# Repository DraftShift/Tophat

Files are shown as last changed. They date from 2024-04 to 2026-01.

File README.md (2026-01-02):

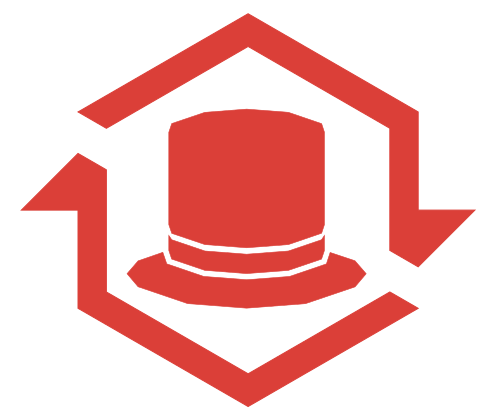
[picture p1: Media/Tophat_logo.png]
#  Tophat 


&nbsp;&nbsp;&nbsp;&nbsp;&nbsp;&nbsp;


## 🌐 Official Website

StealthChanger now has an official website!

👉 **https://stealthchanger.com** 

##
Currently there is only a simplified print it yourself version. This is meant for people not wanting to invest in more extrusions and side plates. you simply have to print the parts. and you can reuse your old top plate and corner pieces.

NOTE, a fully parametric design using extrusions is under design though it will take longer to finalise. The next design will have a bigger focus on adding things like lights, can wiring and other QOL / fancypants features.

### The current height is 200mm tall, check if this is good enough for your purposes!

## Printed part BOM
### 350 - 300
- 56x M3 heat inserts
- 24x M3x10mm SHCS
- 56x M3x8mm SHCS
- 24x M3 T-nut hammerhead

### 250
- 56x M3 heat inserts
- 24x M3x10mm SHCS
- 48x M3x8mm SHCS
- 16x M3 T-nut hammerhead

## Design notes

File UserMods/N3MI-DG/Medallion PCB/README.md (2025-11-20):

# RGB PCB for Stealthchanger Medallion
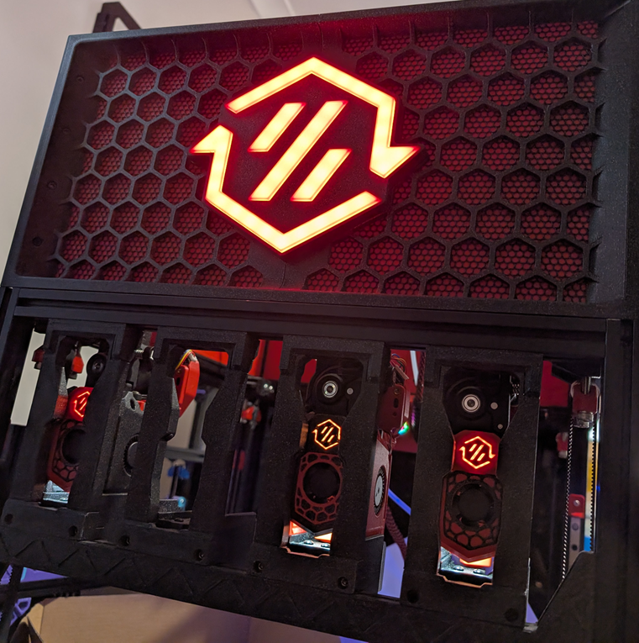
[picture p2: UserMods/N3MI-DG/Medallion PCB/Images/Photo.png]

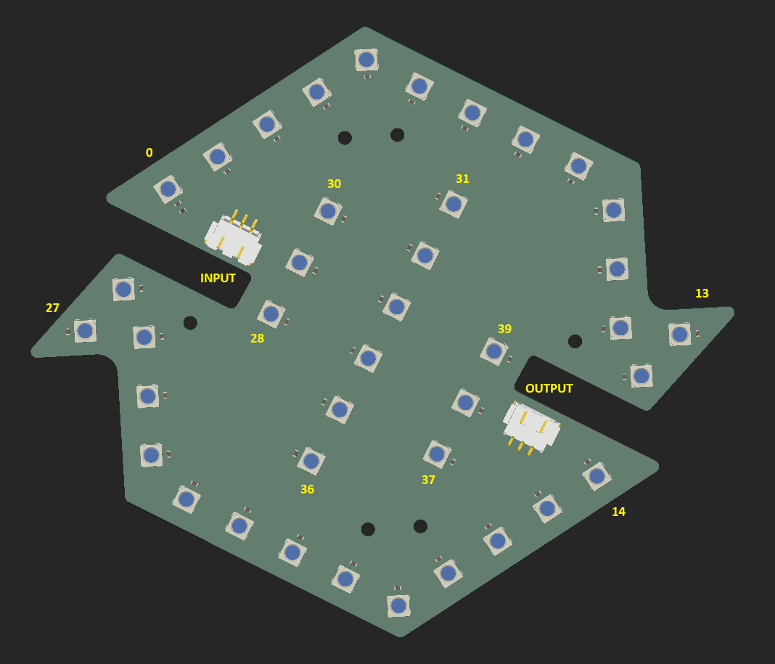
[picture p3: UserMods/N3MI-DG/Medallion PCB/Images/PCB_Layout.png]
PCB Layout


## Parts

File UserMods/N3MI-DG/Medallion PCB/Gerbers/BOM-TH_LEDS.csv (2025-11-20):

Comment | Designator | Footprint | LCSC | Quantity
C0.1uF | C1,C10,C11,C12,C13,C14,C15,C16,C17,C18,C19,C2,C20,C21,C22,C23,C24,C25,C26,C27,C28,C29,C3,C30,C31,C32,C33,C34,C35,C36,C37,C38,C39,C4,C40,C5,C6,C7,C8,C9 | C_0603_1608Metric | C14663 | 40
Conn_01x03_Socket | J1,J2 | JST_XH_S3B-XH-SM4-TB_1x03-1MP_P2.50mm_Horizontal | C161860 | 2
R470 | R1 | R_0603_1608Metric | C23179 | 1
SK6812 | D1,D10,D11,D12,D13,D14,D15,D16,D17,D18,D19,D2,D20,D21,D22,D23,D24,D25,D26,D27,D28,D29,D3,D30,D31,D32,D33,D34,D35,D36,D37,D38,D39,D4,D40,D5,D6,D7,D8,D9 | LED_SK6812_PLCC4_5.0x5.0mm_P3.2mm | C5181320 | 40

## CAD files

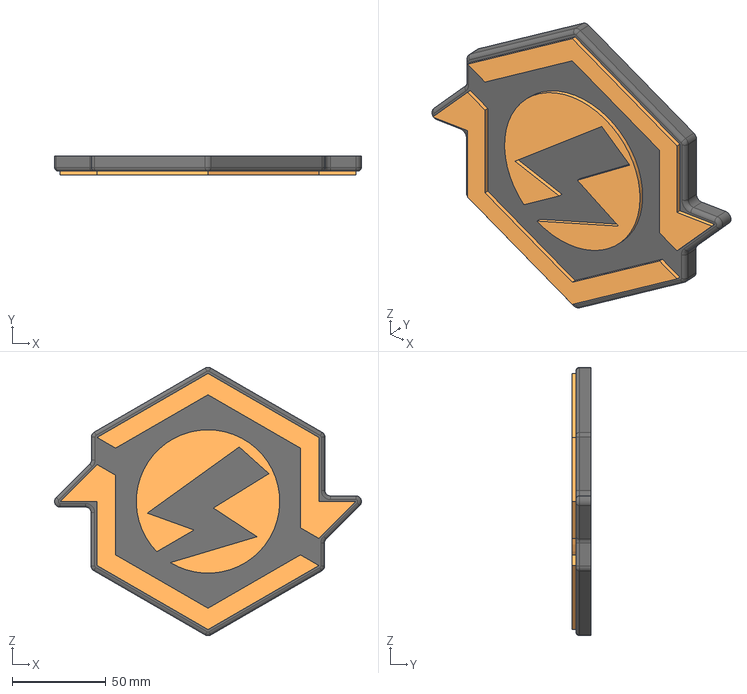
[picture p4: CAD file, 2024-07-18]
Printed version/CAD/Medalion Sovol.step
164.0 x 10.0 x 143.4 mm

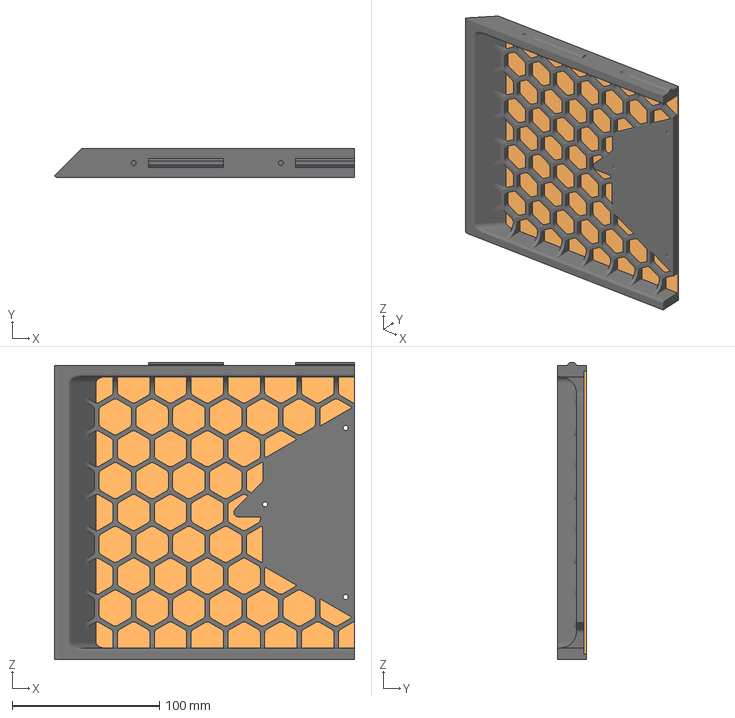
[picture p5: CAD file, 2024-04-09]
Printed version/STLs/250/Side_B_250_x4.3mf
203.8 x 20.0 x 202.0 mm

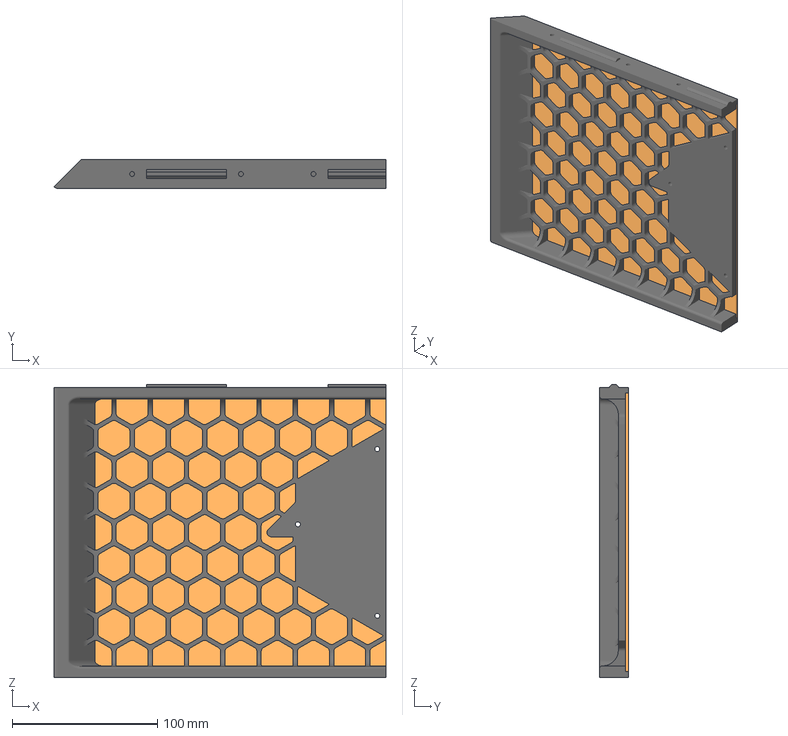
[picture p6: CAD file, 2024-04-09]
Printed version/STLs/300/Side_B_300_x4.3mf
228.8 x 20.0 x 202.0 mm

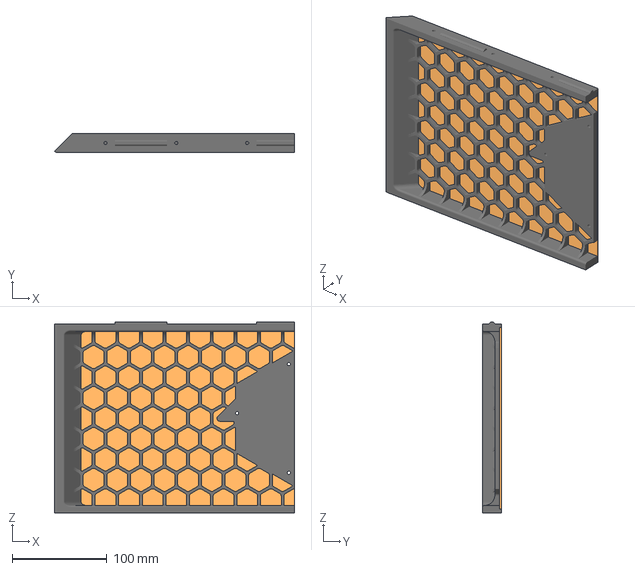
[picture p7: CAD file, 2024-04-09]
Printed version/STLs/350/Side_B_350_x4.3mf
253.8 x 20.0 x 202.0 mm

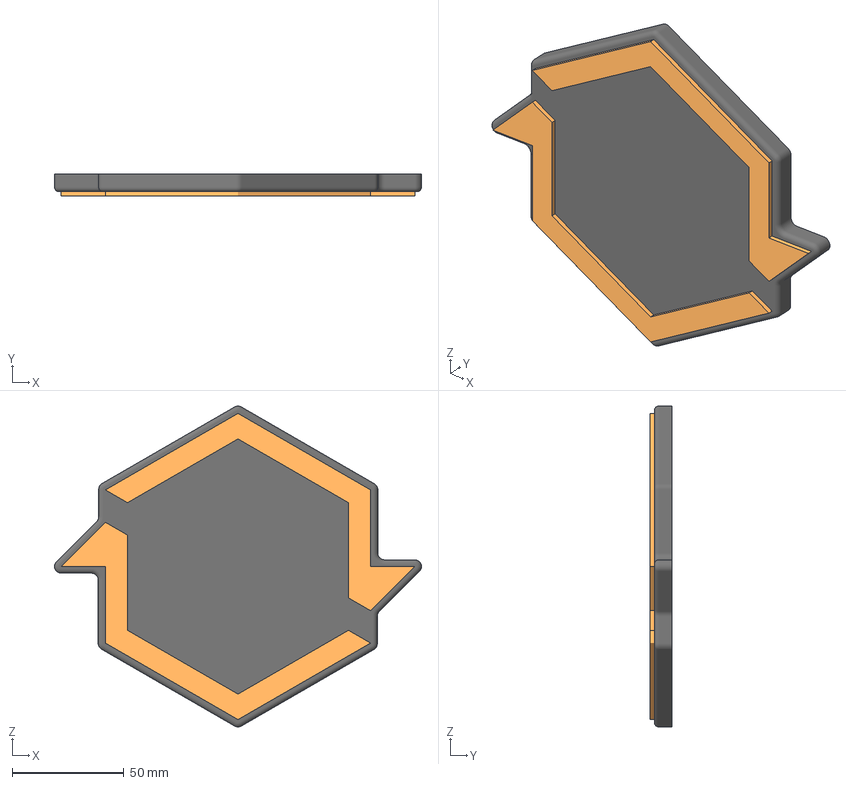
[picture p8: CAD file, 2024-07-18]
Printed version/STLs/Medalion Blank.3mf
164.0 x 10.0 x 143.4 mm

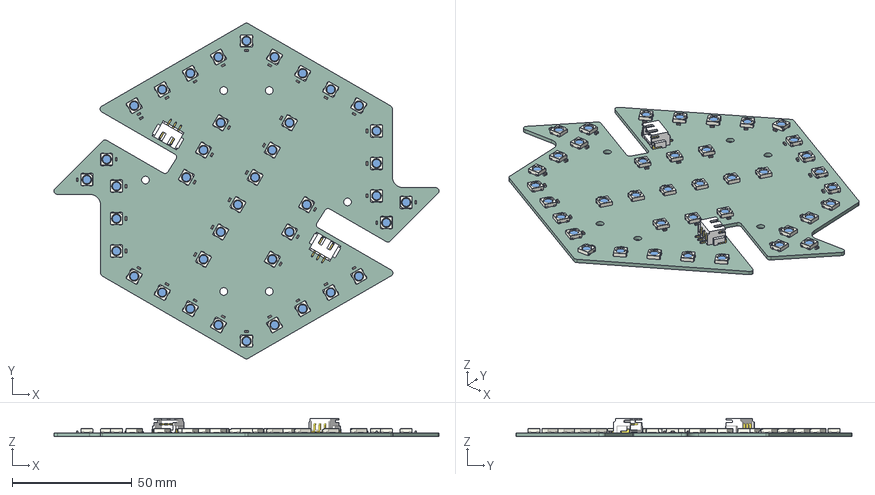
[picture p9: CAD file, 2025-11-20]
UserMods/N3MI-DG/Medallion PCB/Source/TH_LEDS.step
160.8 x 140.2 x 7.59 mm
LED_SK6812_PLCC4_5.0x5.0mm_P3.2mm x 40
C_0603_1608Metric x 40
S3B-XH-SM4-TB x 2
R_0603_1608Metric
TH_LEDS_PCB

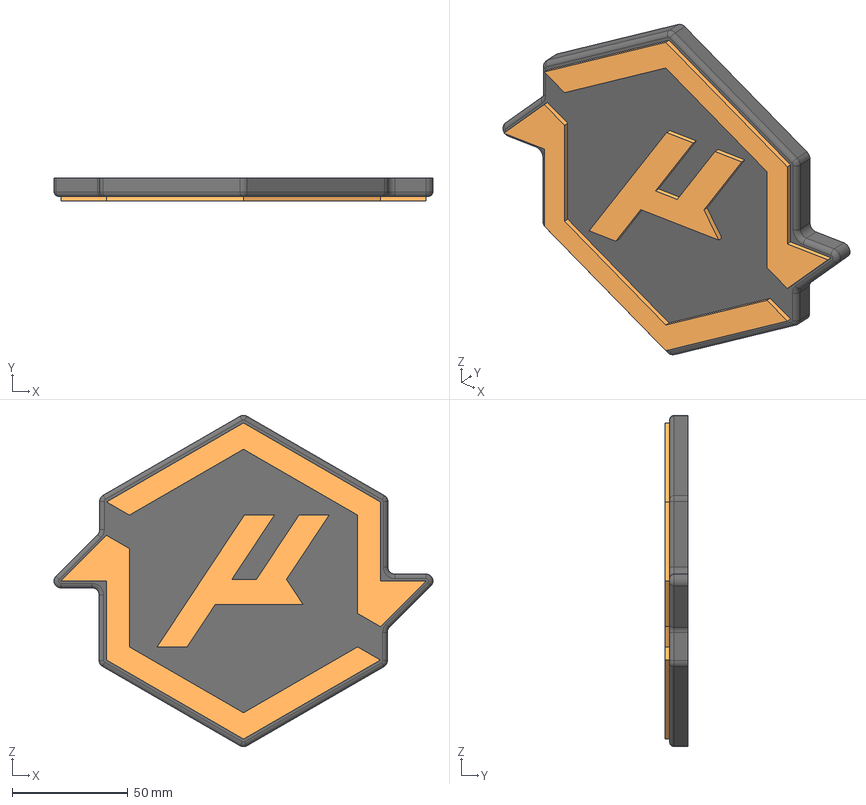
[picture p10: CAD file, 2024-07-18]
Printed version/CAD/Medalion Micron.step
164.0 x 10.0 x 143.4 mm

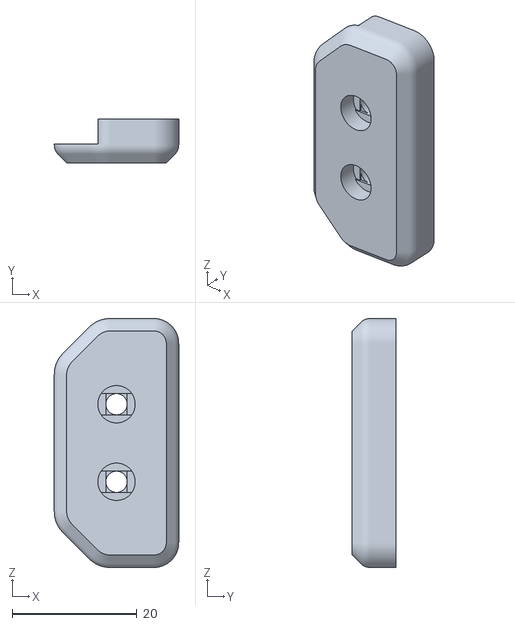
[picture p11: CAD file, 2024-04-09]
Printed version/STLs/Midclip_[a]_x4.stl
20.0 x 7.00 x 40.0

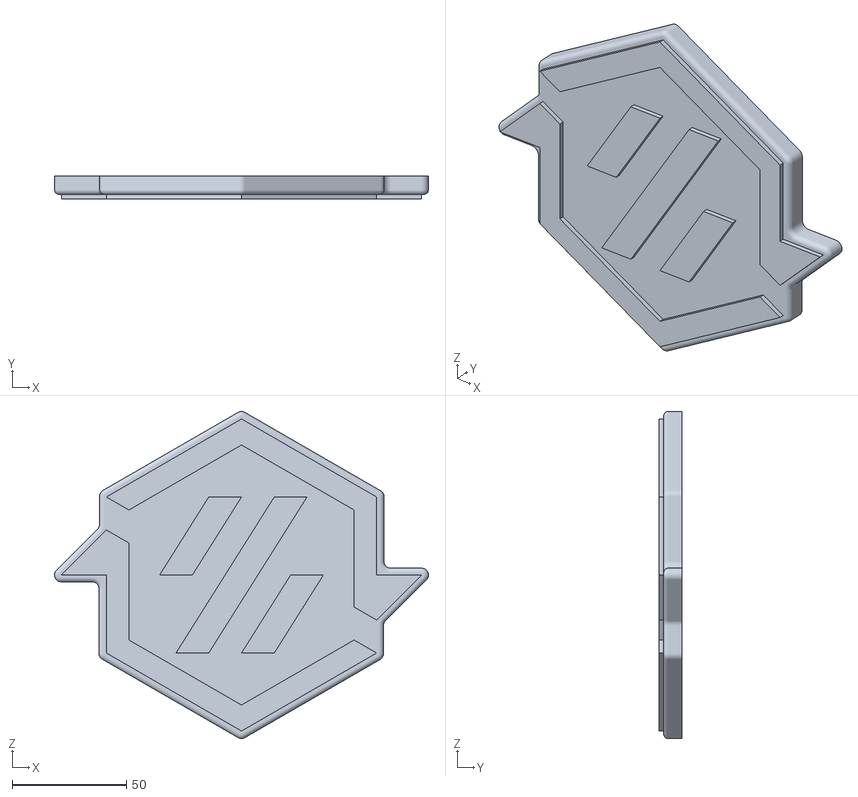
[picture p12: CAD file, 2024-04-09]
Printed version/STLs/Medalion.stl
164.0 x 10.0 x 143.4

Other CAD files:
Printed version/STLs/250/Side_A_250_x4.3mf
Printed version/STLs/300/Side_A_300_x4.3mf
Printed version/STLs/350/Side_A_350_x4.3mf
Printed version/CAD/Medalion Archetype.step
Printed version/CAD/Medalion Blanks.step
Printed version/CAD/Printed_tophat_Medalion.step
Printed version/CAD/Printed_tophat_Medalion.f3d
Printed version/STLs/Medalion Archetype.3mf
Printed version/STLs/Medalion Micron.3mf
Printed version/STLs/Medalion Sovol.3mf

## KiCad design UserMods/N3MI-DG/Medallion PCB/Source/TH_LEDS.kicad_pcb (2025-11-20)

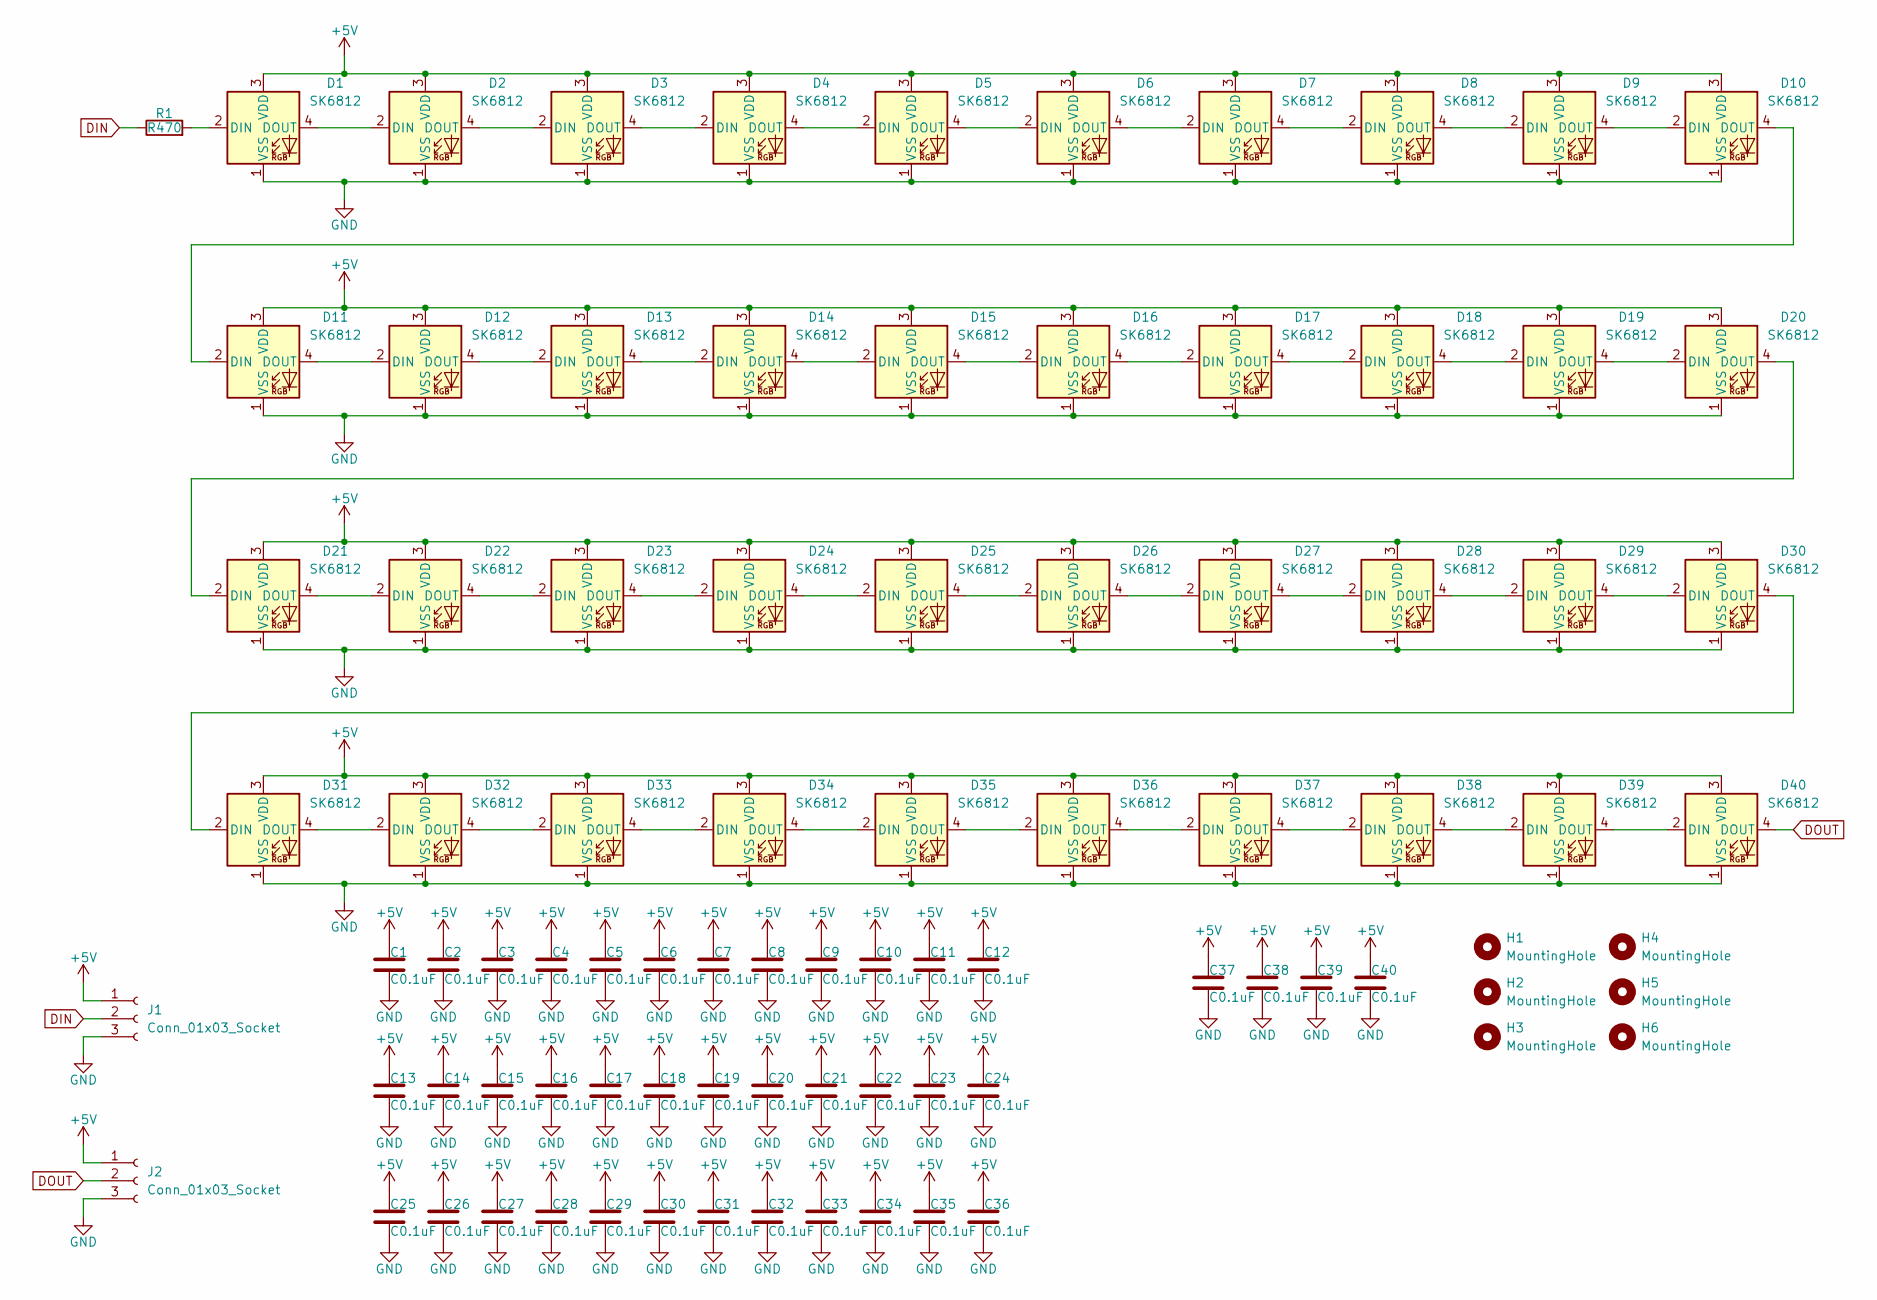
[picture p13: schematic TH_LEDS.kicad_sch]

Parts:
C1, C2, C3, C4, C5, C6, C7, C8, C9, C10, C11, C12, C13, C14, C15, C16, C17, C18, C19, C20, C21, C22, C23, C24, C25, C26, C27, C28, C29, C30, C31, C32, C33, C34, C35, C36, C37, C38, C39, C40: C0.1uF; C_0603_1608Metric
D1, D2, D3, D4, D5, D6, D7, D8, D9, D10, D11, D12, D13, D14, D15, D16, D17, D18, D19, D20, D21, D22, D23, D24, D25, D26, D27, D28, D29, D30, D31, D32, D33, D34, D35, D36, D37, D38, D39, D40: SK6812; LED_SK6812_PLCC4_5.0x5.0mm_P3.2mm
H1, H2, H3, H4, H5, H6: MountingHole; MountingHole_3.2mm_M3_DIN965_Pad
J1, J2: Conn_01x03_Socket; JST_XH_S3B-XH-SM4-TB_1x03-1MP_P2.50mm_Horizontal
R1: R470; R_0603_1608Metric

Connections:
+5V: C1.1, C2.1, C3.1, C4.1, C5.1, C6.1, C7.1, C8.1, C9.1, C10.1, C11.1, C12.1, C13.1, C14.1, C15.1, C16.1, C17.1, C18.1, C19.1, C20.1, C21.1, C22.1, C23.1, C24.1, C25.1, C26.1, C27.1, C28.1, C29.1, C30.1, C31.1, C32.1, C33.1, C34.1, C35.1, C36.1, C37.1, C38.1, C39.1, C40.1, D1.3 (VDD), D2.3 (VDD), D3.3 (VDD), D4.3 (VDD), D5.3 (VDD), D6.3 (VDD), D7.3 (VDD), D8.3 (VDD), D9.3 (VDD), D10.3 (VDD), D11.3 (VDD), D12.3 (VDD), D13.3 (VDD), D14.3 (VDD), D15.3 (VDD), D16.3 (VDD), D17.3 (VDD), D18.3 (VDD), D19.3 (VDD), D20.3 (VDD), D21.3 (VDD), D22.3 (VDD), D23.3 (VDD), D24.3 (VDD), D25.3 (VDD), D26.3 (VDD), D27.3 (VDD), D28.3 (VDD), D29.3 (VDD), D30.3 (VDD), D31.3 (VDD), D32.3 (VDD), D33.3 (VDD), D34.3 (VDD), D35.3 (VDD), D36.3 (VDD), D37.3 (VDD), D38.3 (VDD), D39.3 (VDD), D40.3 (VDD), J1.1, J2.1
DIN: J1.2, R1.1
DOUT: D40.4 (DOUT), J2.2
GND: C1.2, C2.2, C3.2, C4.2, C5.2, C6.2, C7.2, C8.2, C9.2, C10.2, C11.2, C12.2, C13.2, C14.2, C15.2, C16.2, C17.2, C18.2, C19.2, C20.2, C21.2, C22.2, C23.2, C24.2, C25.2, C26.2, C27.2, C28.2, C29.2, C30.2, C31.2, C32.2, C33.2, C34.2, C35.2, C36.2, C37.2, C38.2, C39.2, C40.2, D1.1 (VSS), D2.1 (VSS), D3.1 (VSS), D4.1 (VSS), D5.1 (VSS), D6.1 (VSS), D7.1 (VSS), D8.1 (VSS), D9.1 (VSS), D10.1 (VSS), D11.1 (VSS), D12.1 (VSS), D13.1 (VSS), D14.1 (VSS), D15.1 (VSS), D16.1 (VSS), D17.1 (VSS), D18.1 (VSS), D19.1 (VSS), D20.1 (VSS), D21.1 (VSS), D22.1 (VSS), D23.1 (VSS), D24.1 (VSS), D25.1 (VSS), D26.1 (VSS), D27.1 (VSS), D28.1 (VSS), D29.1 (VSS), D30.1 (VSS), D31.1 (VSS), D32.1 (VSS), D33.1 (VSS), D34.1 (VSS), D35.1 (VSS), D36.1 (VSS), D37.1 (VSS), D38.1 (VSS), D39.1 (VSS), D40.1 (VSS), J1.3, J2.3
unnamed: D1.2 (DIN), R1.2
unnamed: D1.4 (DOUT), D2.2 (DIN)
unnamed: D2.4 (DOUT), D3.2 (DIN)
unnamed: D3.4 (DOUT), D4.2 (DIN)
unnamed: D4.4 (DOUT), D5.2 (DIN)
unnamed: D5.4 (DOUT), D6.2 (DIN)
unnamed: D6.4 (DOUT), D7.2 (DIN)
unnamed: D7.4 (DOUT), D8.2 (DIN)
unnamed: D8.4 (DOUT), D9.2 (DIN)
unnamed: D9.4 (DOUT), D10.2 (DIN)
unnamed: D10.4 (DOUT), D11.2 (DIN)
unnamed: D11.4 (DOUT), D12.2 (DIN)
unnamed: D12.4 (DOUT), D13.2 (DIN)
unnamed: D13.4 (DOUT), D14.2 (DIN)
unnamed: D14.4 (DOUT), D15.2 (DIN)
unnamed: D15.4 (DOUT), D16.2 (DIN)
unnamed: D16.4 (DOUT), D17.2 (DIN)
unnamed: D17.4 (DOUT), D18.2 (DIN)
unnamed: D18.4 (DOUT), D19.2 (DIN)
unnamed: D19.4 (DOUT), D20.2 (DIN)
unnamed: D20.4 (DOUT), D21.2 (DIN)
unnamed: D21.4 (DOUT), D22.2 (DIN)
unnamed: D22.4 (DOUT), D23.2 (DIN)
unnamed: D23.4 (DOUT), D24.2 (DIN)
unnamed: D24.4 (DOUT), D25.2 (DIN)
unnamed: D25.4 (DOUT), D26.2 (DIN)
unnamed: D26.4 (DOUT), D27.2 (DIN)
unnamed: D27.4 (DOUT), D28.2 (DIN)
unnamed: D28.4 (DOUT), D29.2 (DIN)
unnamed: D29.4 (DOUT), D30.2 (DIN)
unnamed: D30.4 (DOUT), D31.2 (DIN)
unnamed: D31.4 (DOUT), D32.2 (DIN)
unnamed: D32.4 (DOUT), D33.2 (DIN)
unnamed: D33.4 (DOUT), D34.2 (DIN)
unnamed: D34.4 (DOUT), D35.2 (DIN)
unnamed: D35.4 (DOUT), D36.2 (DIN)
unnamed: D36.4 (DOUT), D37.2 (DIN)
unnamed: D37.4 (DOUT), D38.2 (DIN)
unnamed: D38.4 (DOUT), D39.2 (DIN)
unnamed: D39.4 (DOUT), D40.2 (DIN)

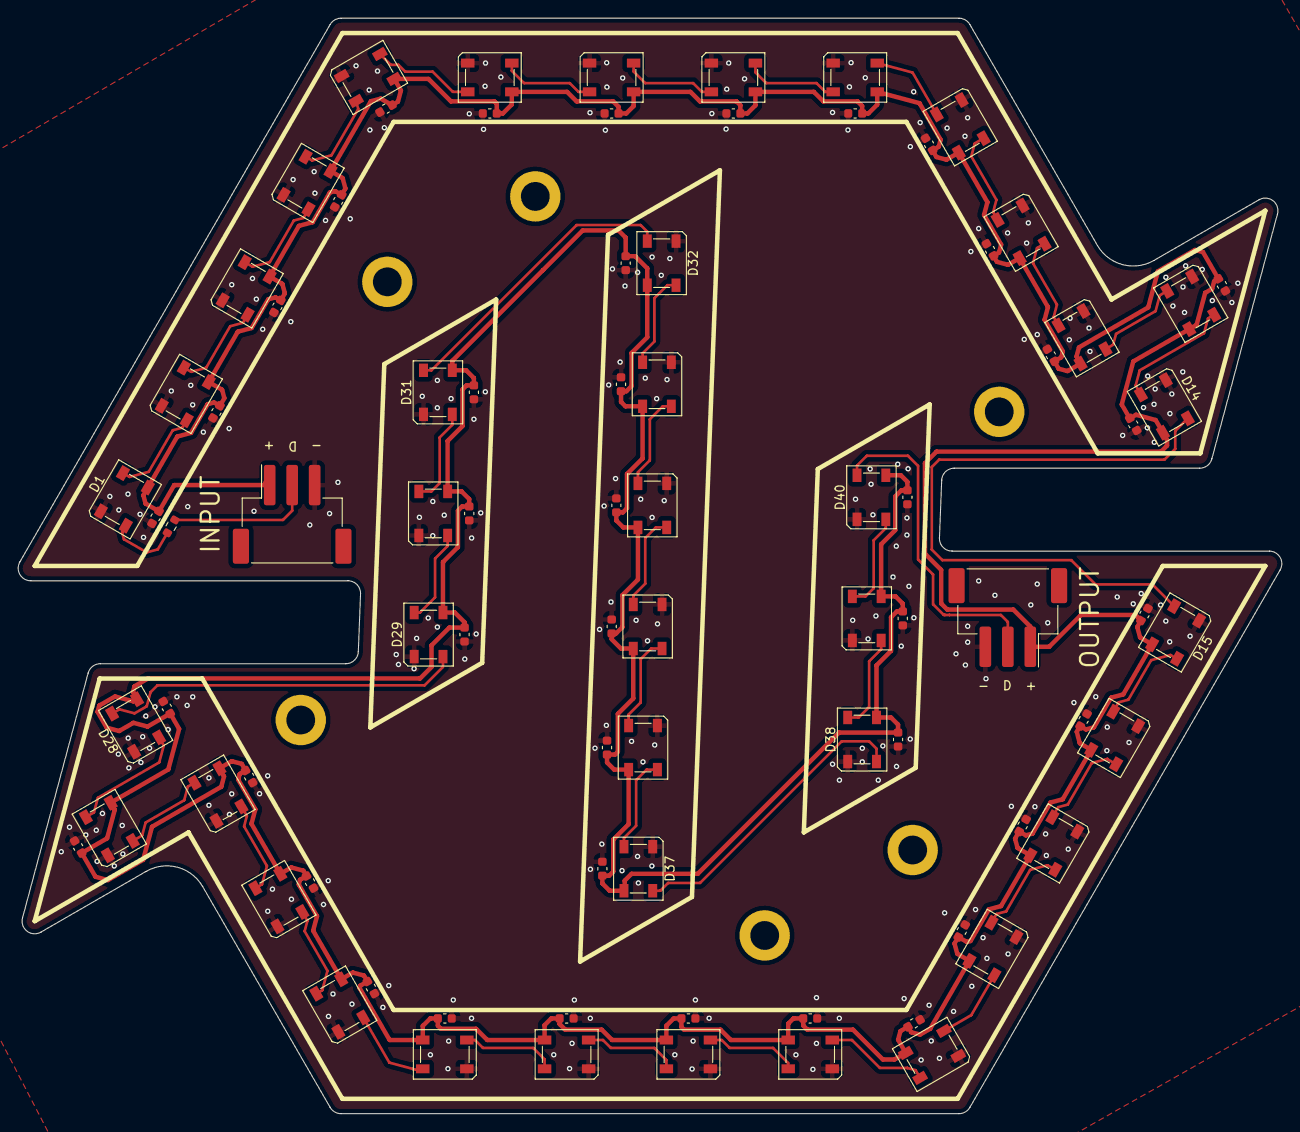
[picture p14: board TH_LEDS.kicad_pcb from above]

Board: 2 copper layers, 140.5 x 121.8 mm, 89 parts (0 on the bottom side), 44 nets.

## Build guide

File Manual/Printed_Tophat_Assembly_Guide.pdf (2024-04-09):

# Printed Tophat

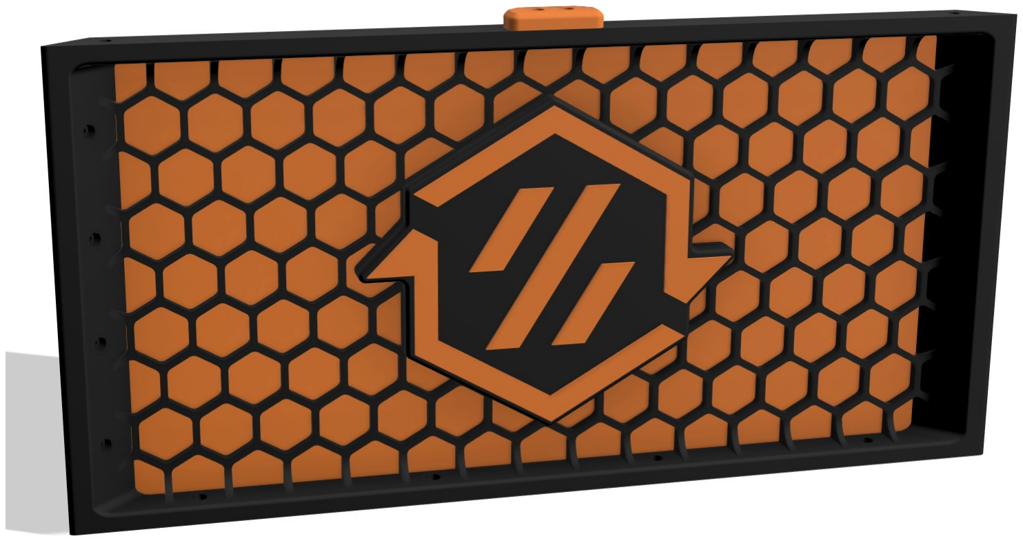
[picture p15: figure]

# Printed Tophat BUILD GUIDE

# When you got too much plastic and dont wana buy extrusions

# VERSION 2024-04-09

## PREFACE

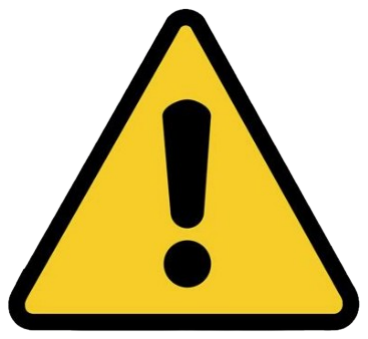
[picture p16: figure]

Before you begin on your journey, a word of caution.

In the comfort of your own home you are about to assemble a robot. This machine can maim, burn, and electrocute you if you are not careful. Please do not become the first STEALTHCHANGER fatality. There is no special Reddit flair for that.

Please, read the entire manual before you start assembly. As you begin wrenching, please check our Discord channels for any tips and questions that may halt your progress.

Most of all, good luck!

THE DRAFTSHIFT TEAM

2

## GITHUB.COM/DRAFTSHIFT/TOPHAT

## TABLE OF CONTENTS

Introduction | 04
Hardware | 07
Heat inserts | 08
Assembly | 9
Attach to frame | 10
Next Steps | 11

3

## INTRODUCTION

PART PRINTING GUIDELINES

The Voron Team has provided the following print guidelines for you to follow in order to have the best chance at success with your parts. The DraftShift Team recommends to follow the same standards. There are often questions about substituting materials or changing printing standards, but we recommend you follow these:

3D PRINTING PROCESS
Fused Deposition Modeling (FDM)

MATERIAL
ABS

LAYER HEIGHT
Recommended: 0.2mm

EXTRUSION WIDTH
Recommended: Forced 0.4mm

INFILL TYPE
Grid, Gyroid, Honeycomb, Triangle or Cubic

INFILL PERCENTAGE
Recommended: 15% or higher

NOTE: These parts do not experience any load an can be less dense compared to other Voron parts

WALL COUNT
Recommended: 4

SOLID TOP/BOTTOM LAYERS
Recommended: 5

4

## INTRODUCTION

FILE NAMING

By this time you should have already downloaded our STL files from the StealthChanger GitHub. You might have noticed that we have used the Voron naming convention for the files. This is how to use them.

PRIMARY COLOUR

Example part_x4.stl

These files will have nothing at the start of the filename.

ACCENT COLOUR

Example [a]_part.stl

We have added “[a]” to the front of any STL file that is intended to be printed with accent colour.

QUANTITY REQUIRED

Example [a]_part_x4.stl

If any file ends with “_x#”, that is telling you the quantity of that part required to build the machine.

HOW TO GET HELP

If you need assistance with your build, we are here to help. Head on over to our Discord group and post your questions. This is our primary medium to help STEALTHCHANGER Users and we have a great community that can help you out if you get stuck.

### https://discord.gg/3G7h3F9TTy

5

## INTRODUCTION

REPORTING ISSUES

Should you find an issue in the documentation or have a suggestion for an improvement please consider opening an issue on GitHub (https://github.com/Stealthchanger/DoorBuffer/issues). When raising an issue please include the relevant page numbers and a short description; annotated screenshots are also very welcome. We periodically update the manual based on the feedback we get.

THIS IS JUST A REFERENCE

This manual is designed to be a simple reference manual and we always recommend downloading the cad-files to look around for yourself.

6

### https://github.com/DraftShift/Tophat

## HARDWARE REFERENCE

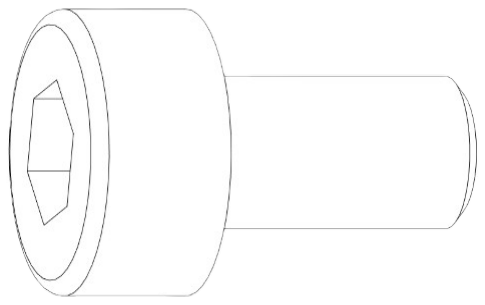
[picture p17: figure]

HEAT SET INSERT Heat inserts with a soldering tip so that they melt the plastic when installed. As the plastic cools, it solidifies around the knurls and ridges on the insert for excellent resistance to both torque and pull-out. | SOCKET HEAD CAP SCREW (SHCS) Metric fastener with a cylindrical head and hex drive. The most common fastener used on the Voron. ISO 4762

T-NUT Hammerhead A type of nut that slides into the extrusion rail as a method of affix other parts to it.

7

## HEAT INSERTS

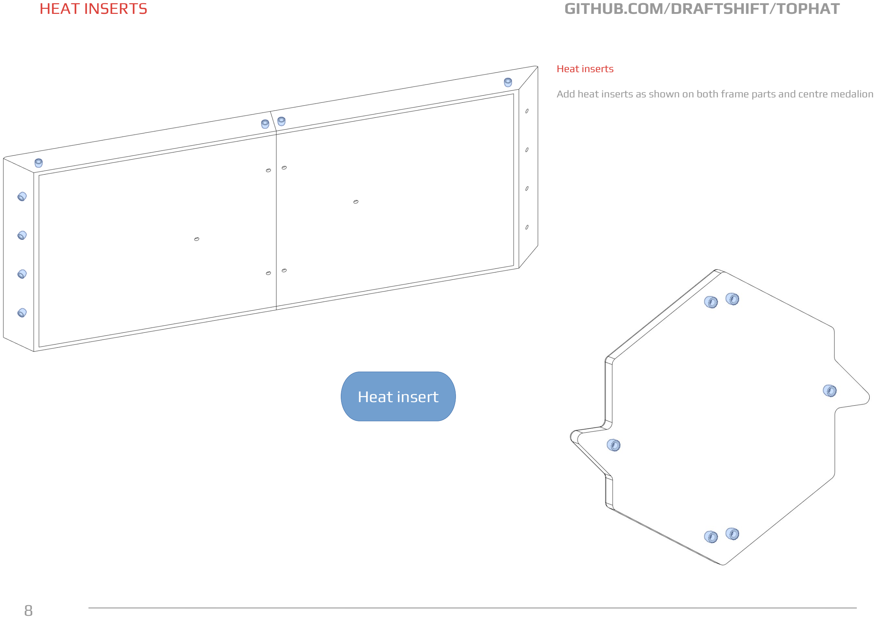
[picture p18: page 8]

Heat inserts

Add heat inserts as shown on both frame parts and centre medalion

8

## Heat insert

## ASSEMBLY

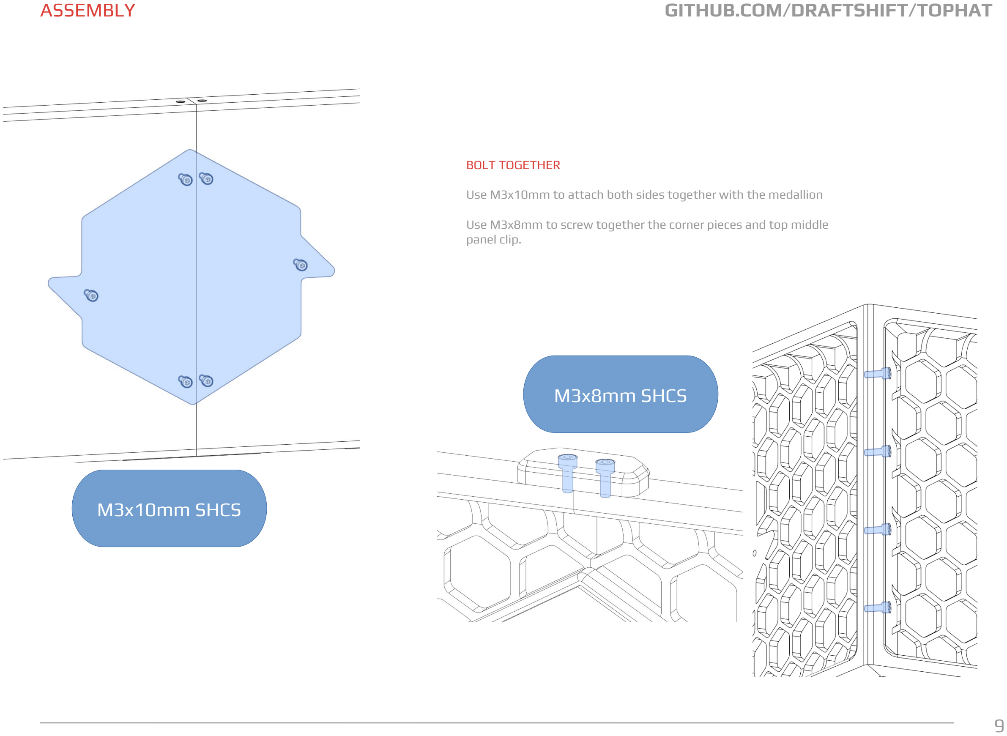
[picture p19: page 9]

BOLT TOGETHER

Use M3x10mm to attach both sides together with the medallion

Use M3x8mm to screw together the corner pieces and top middle panel clip.

## M3x10mm SHCS

9

## M3x8mm SHCS

Screw on to 2020

Repeat all sides 4 times, screw together and bolt down to the top of your printer.

The tophat attaches to your 2020 frame with the same hardware you use for 4mm panel clips. M3x8mm + hammerhead T-NUT

NOTE: You can reuse your old top acrylic panel reusing the 4 corner clips.

## ATTACH TO FRAME

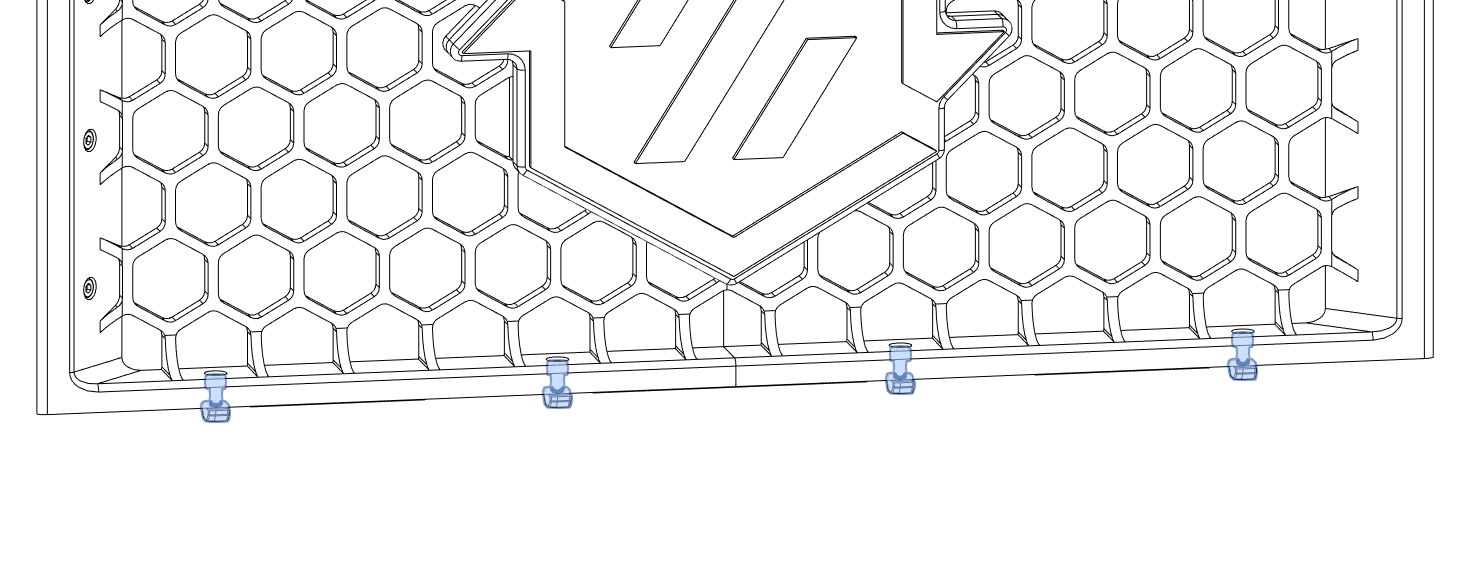
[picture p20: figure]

10

## M3x8 SHCS T-NUT

## NEXT STEPS

ASSEMBLY COMPLETED!

NOTE: In case you forgot to install your modular docks, you can simply loosen the top middle piece and slide in the docks.

NOTE: You can reuse the same top panel corner clips just not the middle ones.

### https://github.com/DraftShift/Tophat

11

Enjoy your new hat

12

## GITHUB.COM/STEALTHCHANGER/TOPHAT

# STEALTHCHANGER

GITHUB

github.com/StealthChanger

DISCORD

discord.gg/3G7h3F9TTy

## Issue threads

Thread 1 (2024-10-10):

Counterbore holes to attach medaillon

gyscos, 2024-10-10:
Hi, and thanks for this design!

The side pieces have holes to screw into the medaillon, but these holes are not counterbored. As a result, the screws there protrude inside the chamber.

There should be enough thickness in the plate to accommodate this?

gyscos, 2024-10-11:
If anyone is interested, I added the counterbores in onshape: [onshape link](https://cad.onshape.com/documents/bea07f443688cc9aed89735d/w/e5c29d4bdbfdc08a5b93622e/e/72ed4d65a69039c803f06629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). It's currently only done for the 350mm version, but should be easy to port to the others.

I'm not a fusion-360 guru though so not sure I could make a PR to fix the f3z file.

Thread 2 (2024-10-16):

Screws for printed BOM seems inaccurate

gyscos, 2024-10-16:
It seems that the screw/heat inserts requirements in the BOM are slightly over-stated.

From what I can tell, the current build needs, for all sizes:

### 56x Heat inserts (currently listed: 64)
* 14x Per side:
  * 4 for the corner
  * 4 on the top for panel clips
  * 6 for the medaillon

### 24x M3x10 screws (currently listed: 36)
* 6x Per side:
  * 6 for the medaillon

Closed 2025-01-02.

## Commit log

2024-04-09 pushed new printed design and manual
    [Medalion.stl, Midclip_[a]_x4.stl, Printed_tophat_Medalion.f3d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]
2024-07-18 Added various logos for medallion
    [Medalion Archetype.3mf, Medalion Blank.3mf, Medalion Micron.3mf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]
2024-07-18 Added CAD files for additional medallions
    [Medalion Archetype.step, Medalion Blanks.step, Medalion Micron.step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]
2025-11-20 Merge pull request #4 from N3MI-DG/PCB
    Medallion PCB
    [BOM-TH_LEDS.csv, TH_LEDS.kicad_pcb, TH_LEDS.kicad_sch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]
2026-01-02 Update README with print version and design plans
    Added information about the simplified print version and future designs.
